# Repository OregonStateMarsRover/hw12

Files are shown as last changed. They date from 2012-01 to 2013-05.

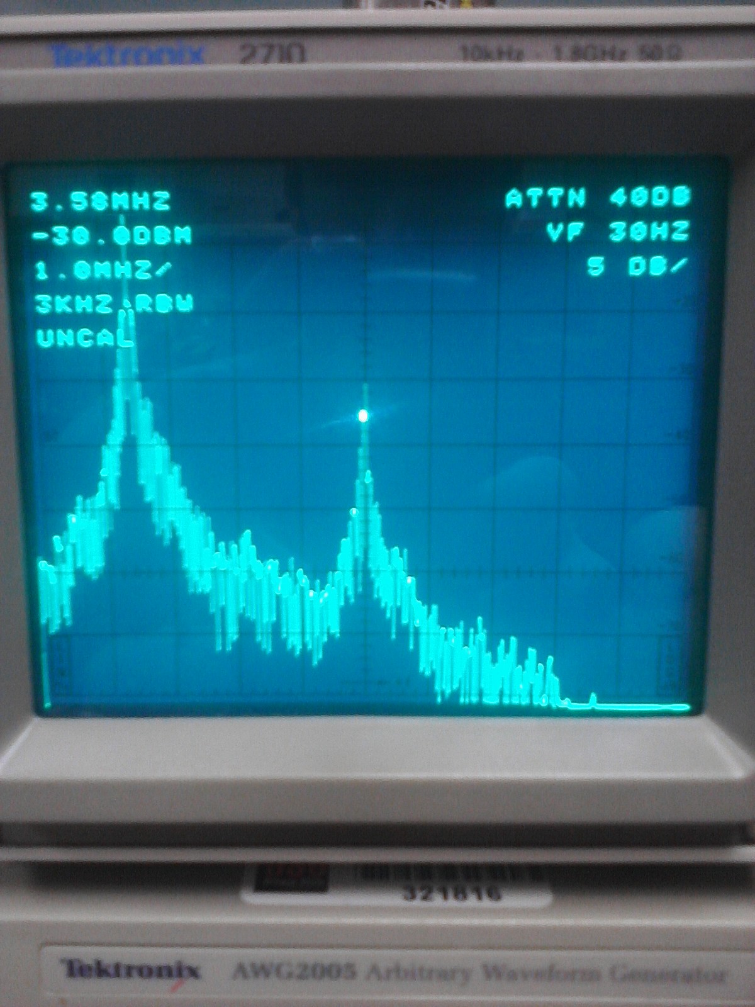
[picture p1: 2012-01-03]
electrical/design/RF&Video/UHF_Video_TX/documents/NTSCSpectrum.jpg

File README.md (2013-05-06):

How this repository is organized
====================

Electrical board documentation
------------------------
This should all be in electrical/design/.
There should be a folder for each board, containing the datasheets for the parts on the board.
There should be PADS drawings, and PDFs of both the schematic and the layout, and a text file BOM.
There should be an explanation of what the board does, and a list of the commercial parts that
it connects to. If there is a good way of linking to the datasheets for these parts, then we
might do that as well.

Commercial parts
-------------------
Parts that aren't custom built (motors, sensors, motor controllers, etc) should be in documents.
These will be further organized by folder.

Currently there are some issues
------------------
Things aren't all where they should be, and often there's three places to look for something.
We're working on that.  However, I don't intend to touch the mechanical folder.

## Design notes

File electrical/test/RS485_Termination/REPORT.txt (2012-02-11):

The purpose of this test is to determine the appropriate method of termination for RS-485 signaling through CAT5 with the SN65HVD32 as
the signal source.

test1a.csv:
	Source Termination: NONE
	Load Termination: 100ohms
	Measurement: Load
	Notes: Almost no ringing. DC current draw 33mA.
test1b.csv:
	Source Termination: NONE
	Load Termination: 100ohms
	Measurement: Source
	Notes: Small overshoot, pretty much as good as it can be.

test2a.csv:
	Source Termination: NONE
	Load Termination: NONE
	Measurement: Load
	Notes: Ringing, 210mV of overshoot.
test2b.csv:
	Source Termination: NONE
	Load Termination: NONE
	Measurement: Source
	Notes: Ringing, 210mV of overshoot.

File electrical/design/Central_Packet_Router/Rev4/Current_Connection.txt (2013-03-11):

Rev 3.
	Daugther Boards
		Motor Drivers
			Back Bogie  (J6)
			Left Bogie  (J12)
			Right Bogie (J7)
			Arm Board   (J2)
	I2C Breakout(Not Used Currently) (J205)
	Random Unused GPIO Pins On Headers (J206 & J207)		
	Freewave Connections (J3)
	UART Wiring
		UART 1: TX and RX Arm
		UART 2: TX and RX Int
		UART 4:	TX and RX Bogie
		UART 5:	TX and RX Freewave

Rev 4.
	Tripod Board
	Arm Contoller

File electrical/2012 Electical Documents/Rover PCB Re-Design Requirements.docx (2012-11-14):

- Tripod
  - redesign audio
  - use better servo connector
  - better video connector solution
  - look at power supply situation
  - reduce size
- Main board
  - remove audio
  - USB interface
  - DMA for GPS data?
    - email Francis about situation
  - No sensors
  - switch to linear regulators
    - simplify power requirements in general
  - Garmin GPS reveiver again

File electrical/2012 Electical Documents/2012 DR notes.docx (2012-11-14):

- CPC
  - Why use an and gate on the bogie RX without drivers with enable?
  - XTAL load capacitor Cl = (C^2/2C)+Cs, 26pF is correct capacitance
- Xbee
  - Reset controlled by MCU?
  - Header on TTL side of serial interface?
  - Test points
  - Thermal vias around LDO?
  - Ferrite beads?
  - AC termination
  - Screw keepouts top and bottom
  - SMA clearance
  - Machine pin header?
- Packet Router
  - Test points
  - Sink LEDs
  - Reset pullup
  - Diode on USB power
  - Series termination
  - Serial Isolation
  - Smaller series resistance on GPIO
  - Discrete resistors for GPIO current limiting
  - Ground USB connector shield
- Motor controller
  - Isolation between itself and sabertooth
  - Hall effect current sensor instead of current sense resistor
  - Smaller fuse
  - Match sabertooth terminal block pattern
  - Consider higher thickness PCB plating
- Solenoid Driver
  - Reduce complexity
  - Relays?

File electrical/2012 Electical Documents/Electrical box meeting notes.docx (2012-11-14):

Try mounting video mux to the top of the FM transmitter.

Try removing the modulator and PA and putting them in another enclosure.

Make faraday cage for mux.

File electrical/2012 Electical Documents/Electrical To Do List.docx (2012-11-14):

- EMI Testing
  - Cody / Tyler
- Main Board Redesign
  - Cody
- Camera Board Redesign
  - Tyler
- Critical Frequency List
  - Cody / Tyler
- Power Consumption Data Sheet
- Dr Hurst NSF Grant
  - Tyler / Delegated to John. Z?
- Figure Out Motor!!!
- Test Small Cameras
  - Tyler
- Test Motor Controllers
  - Cody / Tyler
- Figure Out Connectors
  - Everyone

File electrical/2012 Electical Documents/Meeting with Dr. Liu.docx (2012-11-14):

- Automatic antenna pointing device
  - GPS based angle
- MIMO with best antenna selection circuit
- Possibly implement automatic bitrate scaling
- Don’t try to use davinci
- Come up with repeater system

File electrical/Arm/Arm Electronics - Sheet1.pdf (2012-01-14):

Joint 2
| 2 | Limit Switch | http://www.mouser.com/catalog/specsheets/E51_Series.pdf
| 1 | Gear motor | https://docs.google.com/viewer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
| 1 | Magnetic Encoder (RMB30SI) | http://www.rls.si/document/RMB30D01.pdf

Joint 3
| 1 | 300 deg Potentiometer (P232) | http://www.bitechnologies.com/pdfs/p232.pdf
| 1 | AX-12 | http://www.crustcrawler.com/products/bioloid/docs/AX-12.pdf

Interchangable Joints

Configuration 1 (Equipment Servicing)

| 1 | 300 deg Potentiometer (P232) | http://www.bitechnologies.com/pdfs/p232.pdf
| 1 | AX-12 | http://www.crustcrawler.com/products/bioloid/docs/AX-12.pdf
| 2 | Voltage Reading Plates
| 1 | Vibration Motor | http://www.mouser.com/ProductDetail/Autotrol/052-0010AD/?qs=sGAEpiMZZMvuFyKEiodORsPMp4IpwWQM9fx3Xx3cERs%3d | *This is a 12VDC motor, but we can run it on the 9.5 Rail voltage for the AX-12s
| 3 | Pin Hole Camera | TBD

Configuration 2 (Soil Sample)

| 1 | AX-12 | http://www.crustcrawler.com/products/bioloid/docs/AX-12.pdf
| 1 | Pin Hole Camera | TBD
| QTY. | Part Description | DataSheet
Joint 1
| 2 | Limit Switch | http://www.mouser.com/catalog/specsheets/E51_Series.pdf
| 1 | Gear motor | https://docs.google.com/viewer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
| 1 | Magnetic Encoder (RMB300SI) | http://www.rls.si/document/RMB30D01.pdf

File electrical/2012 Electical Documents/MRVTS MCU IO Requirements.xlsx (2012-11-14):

Function | Interface(s) | GPIO Pins | USARTs | CLK Pins | ADC | '+ | Total GPIO | Total USARTs | Total CLK | Total ADC
Leveling Amplifier Gain | GPIO | 4 |  |  |  | '+ | 30 | 3 | 2 | 4
Leveling Amplifier PED | ADC |  |  |  | 2 | '+
RS485 TRX | UART, GPIO | 2 | 1 |  |  | '+
PLL | SPI, GPIO | 3 | 1 | 1 |  | '+
PLL Lock LED | GPIO | 1 |  |  |  | '+
VSWR OK LED | GPIO | 1 |  |  |  | '+
TEMP OK LED | GPIO | 1 |  |  |  | '+
'+3.6V Enable | GPIO | 1 |  |  |  | '+
'+6V Enable | GPIO | 1 |  |  |  | '+
PA ON LED | GPIO | 1 |  |  |  | '+
MUX | GPIO | 8 |  |  |  | '+
BDC PED | ADC |  |  |  | 2 | '+
TEMP Sensor | SPI | 1 | 1 | 1 |  | '+
PA Enable | GPIO | 1 |  |  |  | '+
PA Gain SEL | GPIO | 4 |  |  |  | '+
Video Buffer Enable | GPIO | 1 |  |  |  | '+
 |  |  |  |  |  | '+
 |  |  |  |  |  | '+
 |  |  |  |  |  | '+
 |  |  |  |  |  | '+
 |  |  |  |  |  | '+
 |  |  |  |  |  | '+
 |  |  |  |  |  | '+
 |  |  |  |  |  | '+
 |  |  |  |  |  | '+
 |  |  |  |  |  | '+
 |  |  |  |  |  | '+
 |  |  |  |  |  | '+
 |  |  |  |  |  | '+
 |  |  |  |  |  | '+
 |  |  |  |  |  | '+
 |  |  |  |  |  | '+
 |  |  |  |  |  | '+
 |  |  |  |  |  | '+
 |  |  |  |  |  | '+
 |  |  |  |  |  | '+
 |  |  |  |  |  | '+
 |  |  |  |  |  | '+
 |  |  |  |  |  | '+
 |  |  |  |  |  | '+
 |  |  |  |  |  | '+
 |  |  |  |  |  | '+
 |  |  |  |  |  | '+
 |  |  |  |  |  | '+
 |  |  |  |  |  | '+
 |  |  |  |  |  | '+
 |  |  |  |  |  | '+
 |  |  |  |  |  | '+
 |  |  |  |  |  | '+
 |  |  |  |  |  | '+
 |  |  |  |  |  | '+
 |  |  |  |  |  | '+
 |  |  |  |  |  | '+
 |  |  |  |  |  | '+
 |  |  |  |  |  | '+
 |  |  |  |  |  | '+
 |  |  |  |  |  | '+
 |  |  |  |  |  | '+
 |  |  |  |  |  | '+
 |  |  |  |  |  | '+
 |  |  |  |  |  | '+
 |  |  |  |  |  | '+
 |  |  |  |  |  | '+
 |  |  |  |  |  | '+
 |  |  |  |  |  | '+
 |  |  |  |  |  | '+
 |  |  |  |  |  | '+
 |  |  |  |  |  | '+
 |  |  |  |  |  | '+
 |  |  |  |  |  | '+
 |  |  |  |  |  | '+
 |  |  |  |  |  | '+
 |  |  |  |  |  | '+
 |  |  |  |  |  | '+
 |  |  |  |  |  | '+
 |  |  |  |  |  | '+
 |  |  |  |  |  | '+
 |  |  |  |  |  | '+
 |  |  |  |  |  | '+
 |  |  |  |  |  | '+
 |  |  |  |  |  | '+
 |  |  |  |  |  | '+
 |  |  |  |  |  | '+
 |  |  |  |  |  | '+
 |  |  |  |  |  | '+
 |  |  |  |  |  | '+
 |  |  |  |  |  | '+
 |  |  |  |  |  | '+
 |  |  |  |  |  | '+
 |  |  |  |  |  | '+
 |  |  |  |  |  | '+
 |  |  |  |  |  | '+
 |  |  |  |  |  | '+
 |  |  |  |  |  | '+
 |  |  |  |  |  | '+
 |  |  |  |  |  | '+
 |  |  |  |  |  | '+
 |  |  |  |  |  | '+
 |  |  |  |  |  | '+
 |  |  |  |  |  | '+
 |  |  |  |  |  | '+
 |  |  |  |  |  | '+
 |  |  |  |  |  | '+

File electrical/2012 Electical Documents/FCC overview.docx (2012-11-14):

Oregon State University

2012 URC

RF Communication Systems & FCC Licensing Overview

Still Image Transmission System

- Communications standard
  - IEEE 802.15.4
- Operating bandwidth
  - 2.4000GHz - 2.4835GHz
- RF transmission in specified bandwidth
  - YES
- RF reception in specified bandwidth
  - YES
- Transmission power
  - +17.8dBm
- Vehicle ERP
  - +23.8dBm
- Base station ERP
  - +29.8dBm
- Duty cycle
  - Intermittent transmission during operation
  - Inactive on demand
- FCC bandwidth allocation
  - ISM
- FCC licensing requirements
  - None

Video Transmission System

- Communications standard
  - Analog FM
- Operating bandwidth
  - 980MHz - 1040MHz
- RF transmission in specified bandwidth
  - YES
- RF reception in specified bandwidth
  - NO
- Transmission power
  - +37dBm
- Vehicle ERP
  - +43dBm
- Duty cycle
  - Always transmitting during operation
  - Inactive on demand
- FCC bandwidth allocation
  - Aeronautical radionavigation
- FCC licensing requirements
  - Technician's license required
  - License holder: Matt Shuman

Control & Telemetry Transmission System

- Communication standard
  - Proprietary FHSS
- Operating bandwidth
  - 2.4000GHz - 2.4835GHz
- Transmission power
  - +30dBm
- Vehicle ERP
  - +36dBm
- Base station ERP
  - +42dBm
- Duty cycle
  - Intermittent transmission during operation
  - Inactive on demand
- FCC bandwidth allocation
  - ISM
- FCC licensing requirements
  - None

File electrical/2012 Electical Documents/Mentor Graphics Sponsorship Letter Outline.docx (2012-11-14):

1 Status of last year’s competition
  a What went poorly
    i Video transmission system
    ii Reliability of motion control system
    iii Operator error
  b What went well
    i Site Survey

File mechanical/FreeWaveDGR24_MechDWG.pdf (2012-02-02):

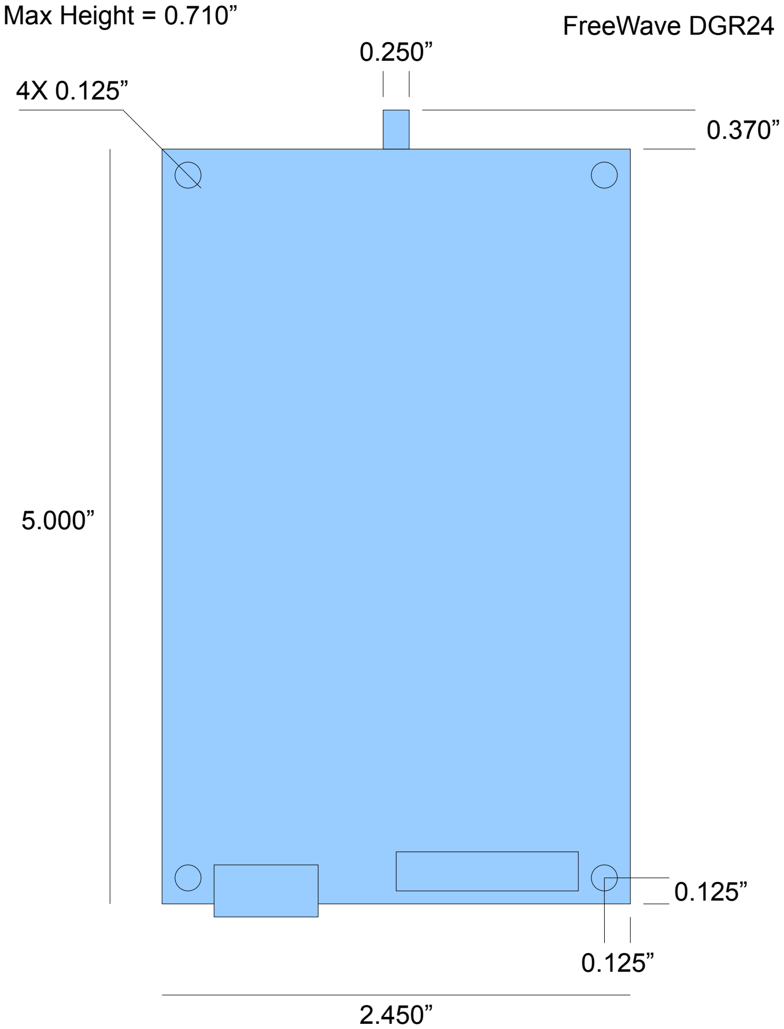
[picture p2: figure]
Max Height = 0.710”; FreeWave DGR24

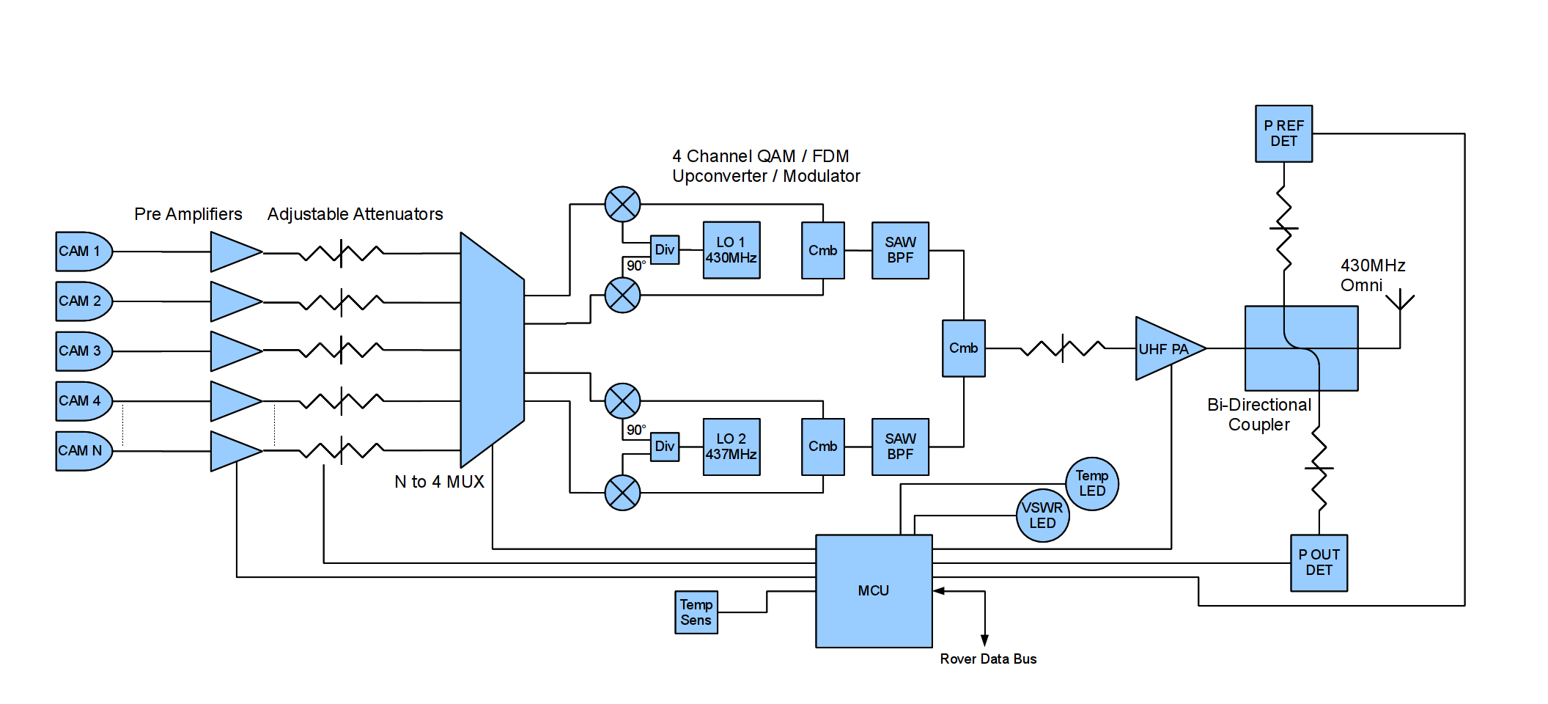
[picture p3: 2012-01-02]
electrical/design/RF&Video/UHF_Video_TX/documents/4channelVideoTX.png

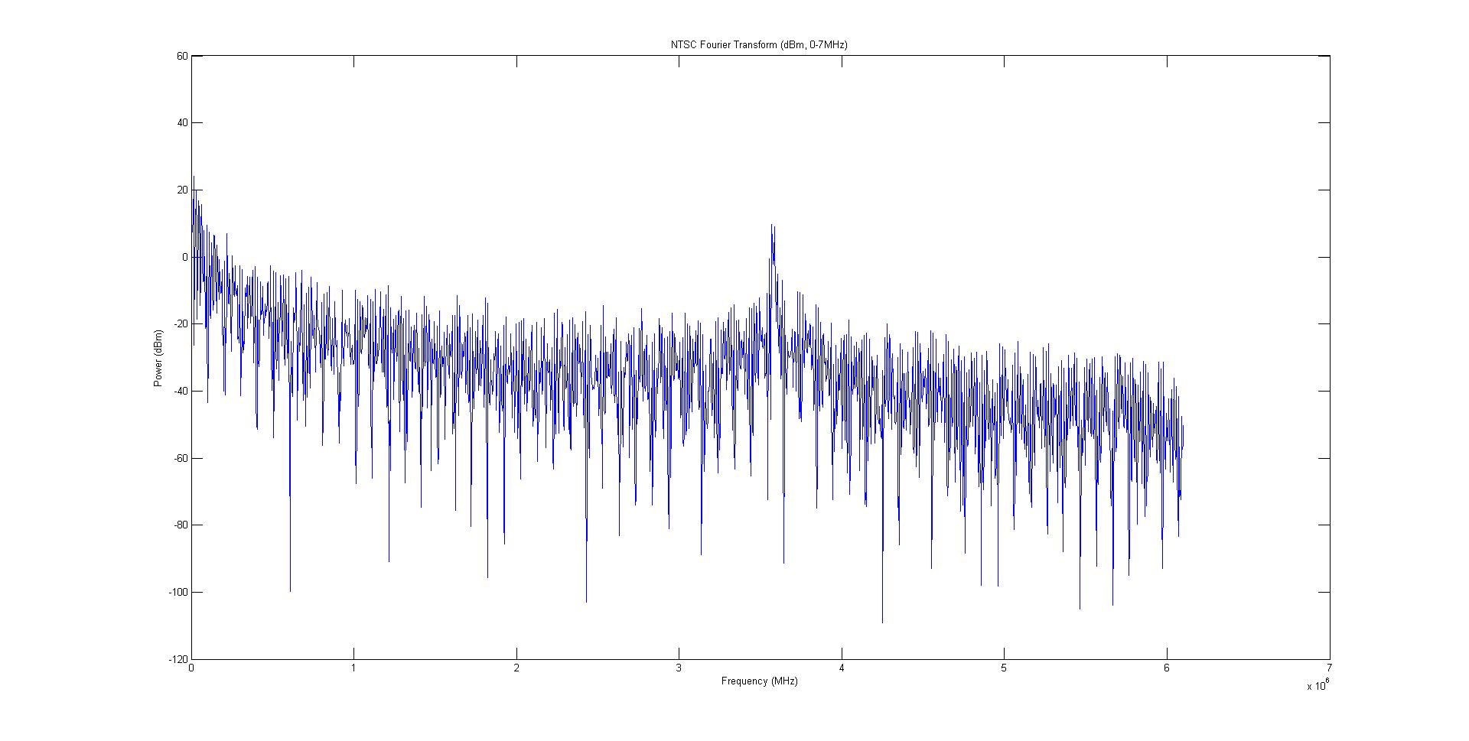
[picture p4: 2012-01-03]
electrical/design/RF&Video/UHF_Video_TX/documents/ntscSpectrum (2).jpg

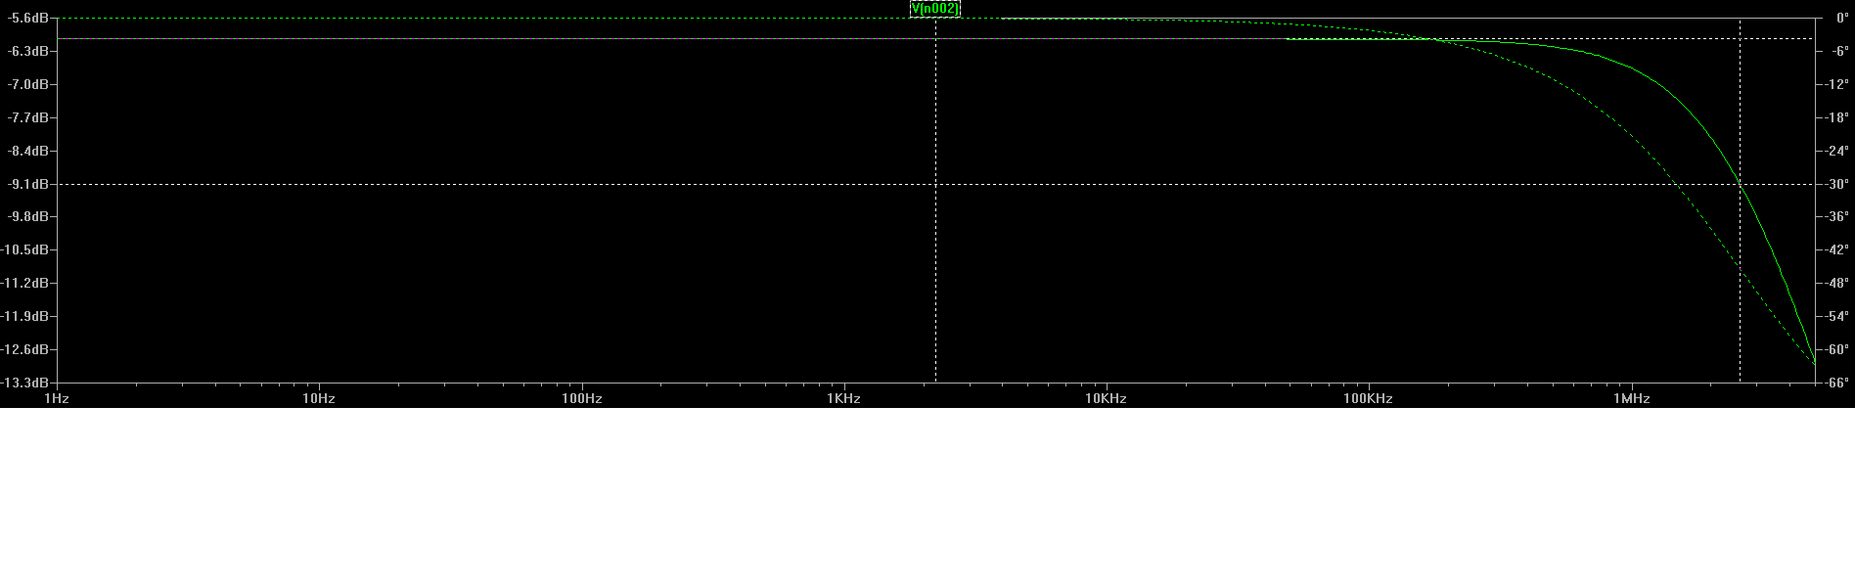
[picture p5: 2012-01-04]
electrical/design/RF&Video/UHF_Video_TX/documents/X9313WSI_bode.png

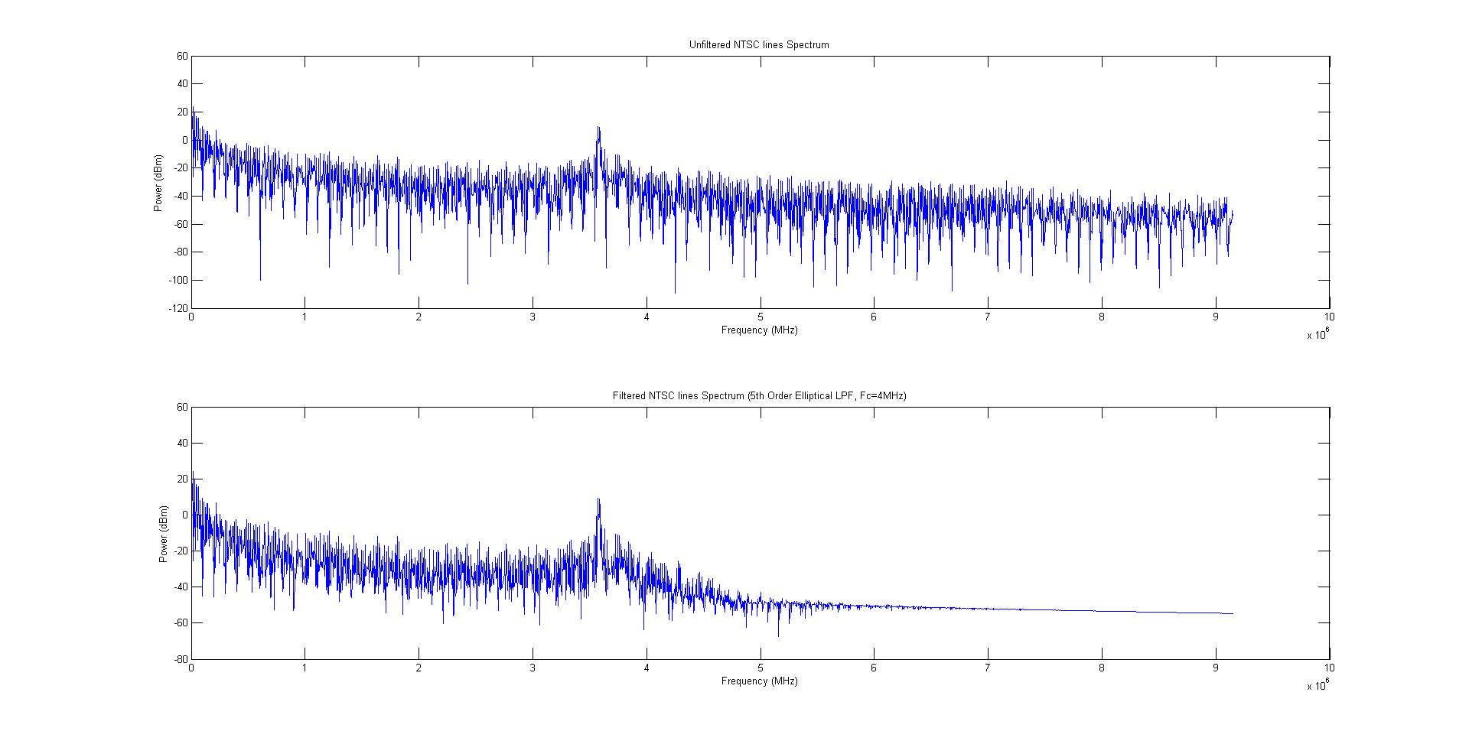
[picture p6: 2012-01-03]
electrical/design/RF&Video/UHF_Video_TX/documents/inputFilter.jpg

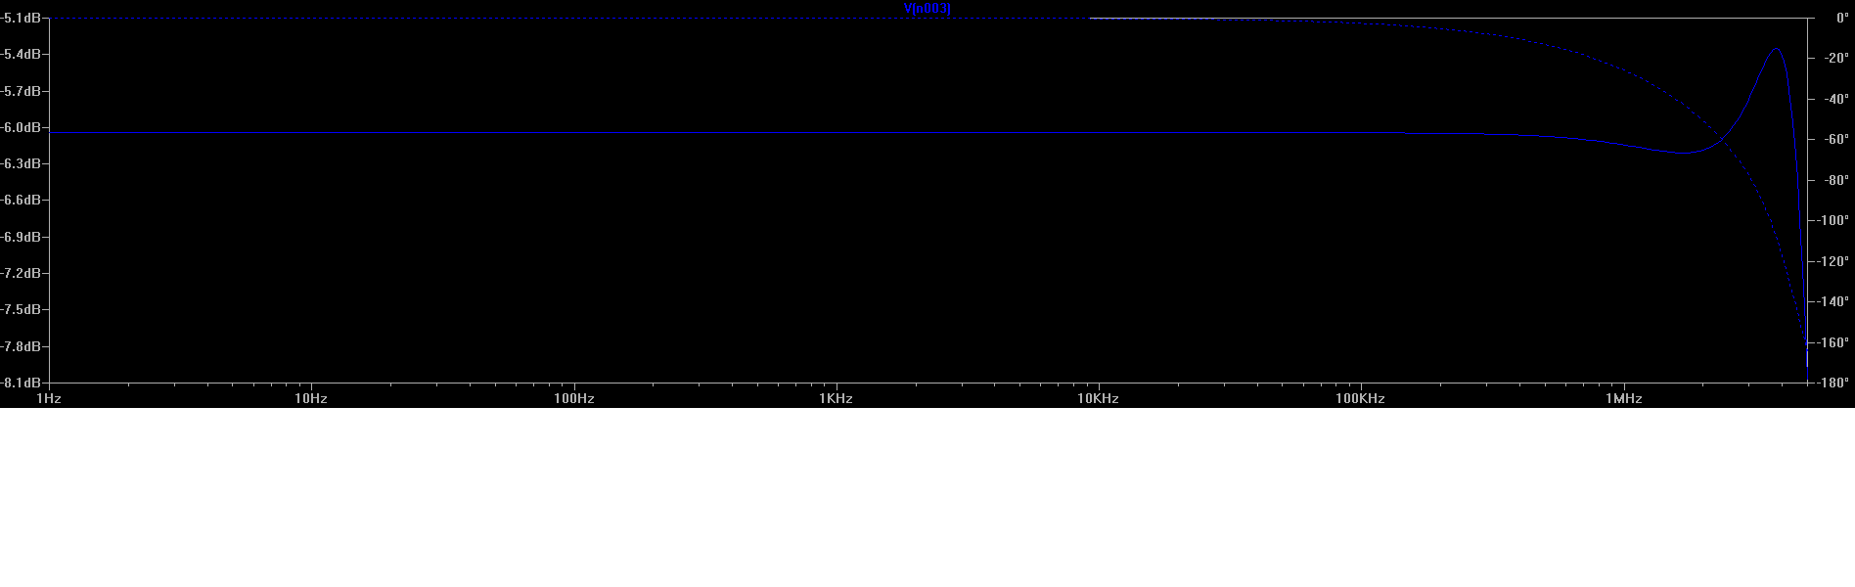
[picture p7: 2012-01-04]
electrical/design/RF&Video/UHF_Video_TX/documents/X9313WSI_compensated_bode.png

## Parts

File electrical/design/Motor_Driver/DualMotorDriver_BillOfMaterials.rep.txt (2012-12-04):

|-----------------------------------------------------------------------|
|Bill Of Materials for DualMotorDriver.sch on Tue Dec 04 11:28:17 2012  |
|-----------------------------------------------------------------------|
|Item|Qty |Reference|Part Name     |Description                  |Value |
|----+----+---------+--------------+-----------------------------+------|
|1   |1   |Y1       |ABL-16.000MHZ-|XTAL, THT, 16.000MHz         |16.000|
|    |    |         |B2,16.000MHz  |                             |MHz   |
|2   |1   |L1       |ACML-0603-190 |Ferrite Bead, 0603           |      |
|3   |1   |U1       |ATXMEGA16D4   |ATxmega D4 series MCU - 16k  |      |
|    |    |         |              |flash                        |      |
|4   |11  |C1-4 C9  |CAP-0603,0.1uF|Capacitor, SMT, 0603         |0.1uF |
|    |    |C11-13   |              |                             |      |
|    |    |C308     |              |                             |      |
|    |    |C310-311 |              |                             |      |
|5   |1   |C306     |CAP-0603,1.2nF|Capacitor, SMT, 0603         |1.2nF |
|6   |4   |C20-23   |CAP-0603,10pF |Capacitor, SMT, 0603         |10pF  |
|7   |1   |C305     |CAP-0603,15nF |Capacitor, SMT, 0603         |15nF  |
|8   |2   |C7-8     |CAP-0603,18pF |Capacitor, SMT, 0603         |18pF  |
|9   |1   |C307     |CAP-0603,1pF  |Capacitor, SMT, 0603         |1pF   |
|10  |1   |C10      |CAP-0603,1uF  |Capacitor, SMT, 0603         |1uF   |
|11  |2   |C5-6     |CAP-0603,4.7uF|Capacitor, SMT, 0603         |4.7uF |
|12  |2   |C309 C312|CAP-1206,10uF |SURFACE MOUNT CAPACITOR 0.062|10uF  |
|    |    |         |              |X 0.126 INCHES               |      |
|13  |4   |C16-19   |CAP-1206,4.7uF|SURFACE MOUNT CAPACITOR 0.062|4.7uF |
|    |    |         |              |X 0.126 INCHES               |      |
|14  |1   |C304     |CAP-1210,4.7uF|Capacitor, SMT, 1206         |4.7uF |
|15  |2   |C24-25   |CAP-RADIAL-10X|Radial Electrolytic          |470uF |
|    |    |         |12.5_3MMP,    |Capacitor, 10x12.5x3mm       |      |
|    |    |         |470uF         |(DxHxP)                      |      |
|16  |1   |C303     |CAP-RADIAL-6.3|Radial Electrolytic          |NU    |
|    |    |         |X7_2.5MMP,NU  |Capacitor, 6.3x7x2.5mm       |      |
|    |    |         |              |(DxHxP)                      |      |
|17  |1   |F1       |FUSE_HOLDER_35|Automotive Fuse Holder       |      |
|    |    |         |44-2          |                             |      |
|18  |3   |J3       |HDR_2P1R_100MI|Standard 2 Pin 1 Row .100"   |      |
|    |    |T300-301 |L             |Header                       |      |
|19  |1   |J1       |HDR_PDI_6_COMP|Header, 6P 2 Row, Through    |      |
|    |    |         |ACT           |Hole, Shroded, 100x100mil,   |      |
|    |    |         |              |for ISP-6 Programming        |      |
|20  |1   |J2       |HDR_SHERLOCK_5|Molex Sherlock 2.0mm         |      |
|    |    |         |P_V           |Header-5P Vertical           |      |
|21  |2   |J5 J300  |HDR_TERMBLOCK_|Screw Terminal Block,        |      |
|    |    |         |5MM-2P        |Horizontal, 5mm, 2 pos.      |      |
|22  |1   |U3       |HIP4082IBZ    |Full Bridge NMOS Gate Driver |      |
|23  |1   |L300     |IND_ELL-6UH470|47uH SMT inductor, shielded, |47uH  |
|    |    |         |M,47uH        |900mA max DC                 |      |
|24  |1   |U4       |MAX4372T      |High-side current sense      |      |
|    |    |         |              |amplifier, 0-28V             |      |
|25  |4   |X1-4     |PHOLE-#4      |Mounting Hole #4 Screw       |      |
|26  |4   |Q1-4     |PSMN011-80YS  |N-Ch MOSFET, 80V 67A 11mOhm, |      |
|    |    |         |              |LFPAK                        |      |
|27  |4   |R3-4 R7-8|RES-0603,1    |SURFACE MOUNT RESISTOR 0.031 |1     |
|    |    |         |              |X 0.061 INCHES, 1/10W        |      |
|28  |2   |R1 R10   |RES-0603,100k |SURFACE MOUNT RESISTOR 0.031 |100k  |
|    |    |         |              |X 0.061 INCHES, 1/10W        |      |
|29  |1   |R5       |RES-0603,10K  |SURFACE MOUNT RESISTOR 0.031 |10K   |
|    |    |         |              |X 0.061 INCHES, 1/10W        |      |
|30  |1   |R305     |RES-0603,10k  |SURFACE MOUNT RESISTOR 0.031 |10k   |
|    |    |         |              |X 0.061 INCHES, 1/10W        |      |
|31  |1   |R302     |RES-0603,165k |SURFACE MOUNT RESISTOR 0.031 |165k  |
|    |    |         |              |X 0.061 INCHES, 1/10W        |      |
|32  |2   |R303-304 |RES-0603,53.6k|SURFACE MOUNT RESISTOR 0.031 |53.6k |
|    |    |         |              |X 0.061 INCHES, 1/10W        |      |
|33  |2   |R9 R11   |RES-0603,5k   |SURFACE MOUNT RESISTOR 0.031 |5k    |
|    |    |         |              |X 0.061 INCHES, 1/10W        |      |
|34  |1   |R6       |RES-0603,???  |SURFACE MOUNT RESISTOR 0.031 |???   |
|    |    |         |              |X 0.061 INCHES, 1/10W        |      |
|35  |1   |R2       |RES-2512,0.01 |2512 SMD Resistor            |0.01  |
|36  |5   |D1-4 D300|SCH_CD214A-B36|Diode, Schottky, 3A 60V, SMA |0.7V  |
|    |    |         |0LF,0.7V      |                             |      |
|37  |2   |D5-6     |SCH_PMEG6002EJ|Schottky Diode, 60V, 2.75A,  |      |
|    |    |         |              |SOD-323F                     |      |
|38  |1   |U2       |SN65HVD32     |TXR,485 Full Duplex          |      |
|39  |1   |S1       |SW_SPST_SWT6-E|Tactile Pushbutton, SPST, 6mm|      |
|    |    |         |5M            |                             |      |
|40  |1   |U301     |TPS5401       |Integrated Buck Converter,   |      |
|    |    |         |              |0.5A Max, 42V In Max         |      |
|41  |1   |U302     |TPS79333      |3.3V LDO, 200mA Maximum      |      |
|    |    |         |              |current                      |      |
|-----------------------------------------------------------------------|

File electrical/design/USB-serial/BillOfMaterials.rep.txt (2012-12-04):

|-----------------------------------------------------------------------|
|Bill Of Materials for usb-serial1.sch on Tue Dec 04 11:32:23 2012      |
|-----------------------------------------------------------------------|
|Item|Qty |Reference|Part Name     |Description                  |Value |
|----+----+---------+--------------+-----------------------------+------|
|1   |8   |C1-8     |CAP-0603,0.1uF|Capacitor, SMT, 0603         |0.1uF |
|2   |1   |U1       |FT230XS-R     |USB-Serial UART Bridge,      |      |
|    |    |         |              |SSOP-16                      |      |
|3   |1   |J7       |HDR_1R4P_100MI|100 mil 4x1 header footprint |      |
|    |    |         |L             |                             |      |
|4   |5   |J2-4 J6  |HDR_2P1R_100MI|Standard 2 Pin 1 Row .100"   |      |
|    |    |J8       |L             |Header                       |      |
|5   |1   |J5       |HDR_SHERLOCK_5|Molex Sherlock 2.0mm         |      |
|    |    |         |P_RA          |Header-5P Vertical           |      |
|6   |1   |J1       |HDR_USB_154-15|USB Header Mini-B Type,      |      |
|    |    |         |320-E         |Female                       |      |
|7   |1   |J9       |K22X-E9P-N    |Header, DE9, Male, Right     |      |
|    |    |         |              |Angle Through Hole           |      |
|8   |3   |D1-3     |LED_0603_GREEN|LED, 0603, Green             |      |
|9   |2   |R7-8     |RES-0603,10k  |SURFACE MOUNT RESISTOR 0.031 |10k   |
|    |    |         |              |X 0.061 INCHES, 1/10W        |      |
|10  |2   |R1-2     |RES-0603,22   |SURFACE MOUNT RESISTOR 0.031 |22    |
|    |    |         |              |X 0.061 INCHES, 1/10W        |      |
|11  |3   |R4-6     |RES-0603,500  |SURFACE MOUNT RESISTOR 0.031 |500   |
|    |    |         |              |X 0.061 INCHES, 1/10W        |      |
|12  |1   |R3       |RES-0603,RT   |SURFACE MOUNT RESISTOR 0.031 |RT    |
|    |    |         |              |X 0.061 INCHES, 1/10W        |      |
|13  |1   |U2       |SN65HVD35     |Full Duplex RS-485           |      |
|    |    |         |              |Transceiver w/ Enables, 3.3V,|      |
|    |    |         |              |SOIC14                       |      |
|14  |1   |U3       |TRS3221E      |RS-232 Line Driver, 1MBps,   |      |
|    |    |         |              |3-5.5V VCC                   |      |
|-----------------------------------------------------------------------|

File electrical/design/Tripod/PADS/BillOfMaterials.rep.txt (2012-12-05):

|-----------------------------------------------------------------------|
|Bill Of Materials for tripod.sch on Tue Nov 27 16:17:03 2012           |
|-----------------------------------------------------------------------|
|Item|Qty |Reference|Part Name     |Description                  |Value |
|----+----+---------+--------------+-----------------------------+------|
|1   |1   |J2       |142146-75     |SMB, Right Angle             |      |No
|2   |1   |U33      |74LVC1G126GV  |Buffer, Tri-State, Single    |      |No
|3   |1   |Y1       |ABM2-16.000MHZ|Crystal                      |      |Yes
|    |    |         |-D4Y-T        |                             |      |
|4   |1   |M1       |AOM-6545P-R   |                             |      |Yes
|5   |1   |U4       |ATXMEGA128A3  |MCU, 8/16b,AVR,              |      |Yes
|    |    |         |              |ATXMega128A3AU               |      |
|6   |21  |D1 D3-12 |B72500D0050A06|Bidirectional TVS Diode      |      |Yes
|    |    |D14-16   |0             |                             |      |
|    |    |D18-24   |              |                             |      |
|7   |1   |U3       |BMP085        |Barometric Pressure Sensor   |      |No
|8   |16  |C3-6     |CAP-0603,     |Capacitor                    |0.1uF |No
|    |    |C15-16   |0.1uF,10%     |                             |      |
|    |    |C24 C33  |              |                             |      |
|    |    |C43-47   |              |                             |      |
|    |    |C105 C111|              |                             |      |
|    |    |C116     |              |                             |      |
|9   |2   |C103 C109|CAP-0603,10nF,|Capacitor                    |10nF  |
|    |    |         |5%            |                             |      |
|10  |7   |C7-8     |CAP-0603,10uF,|Capacitor                    |10uF  |
|    |    |C10-13   |10%           |                             |      |
|    |    |C19      |              |                             |      |
|11  |2   |C22 C25  |CAP-0603,22nF,|Capacitor                    |22nF  |
|    |    |         |20%           |                             |      |
|12  |3   |C1-2 C51 |CAP-0603,27pF,|Capacitor                    |27pF  |
|    |    |         |5%            |                             |      |
|13  |2   |C9 C20   |CAP-0603,     |Capacitor                    |4.7uF |
|    |    |         |4.7uF,20%     |                             |      |
|14  |2   |C17 C23  |CAP-0805,10uF,|Capacitor                    |10uF  |
|    |    |         |10%           |                             |      |
|15  |2   |C26-27   |CAP-0805,1uF, |Capacitor                    |1uF   |
|    |    |         |10%           |                             |      |
|16  |3   |C104 C110|CAP-1206,10uF,|Capacitor                    |10uF  |
|    |    |C113     |10%           |                             |      |
|17  |3   |C14 C18  |CAP_RAD_10X16M|Capacitor                    |470uF |
|    |    |C21      |M,470uF,20%   |                             |      |
|18  |1   |L1       |CHOKE,39mH,5% |Choke, Sheilded              |39mH  |No
|19  |1   |U5       |DRV135        |Balanced Audio Line Driver   |      |Yes
|20  |1   |J1       |FFC_6200097   |                             |      |
|21  |1   |J5       |HDR_MINIFIT_2R|Header, 4 Pin 2 Row Minifit  |      |
|    |    |         |4P_RA         |4.2mm Pitch, Right Angle     |      |
|22  |1   |J28      |HDR_PDI_6     |Header, 6P 2 Row, Through    |      |
|    |    |         |              |Hole, Shroded, 100x100mil,   |      |
|    |    |         |              |for ISP-6 Programming        |      |
|23  |1   |J3       |HDR_SHERLOCK_3|Molex Sherlock 2.0mm         |      |
|    |    |         |P_RA          |Header-3P Vertical           |      |
|24  |1   |J204     |HDR_SHERLOCK_5|Molex Sherlock 2.0mm         |      |
|    |    |         |P_V           |Header-5P Vertical           |      |
|25  |1   |J4       |HDR_SPOX_3P_V |Header, SPOX, 3P1R           |      |
|26  |1   |U35      |KXUD9-4100    |3 Axis Differential          |      |No
|    |    |         |              |Accertlerometer                |      |
|27  |3   |D2 D25   |LED-0805_DIALI|LED, 0805, Red               |      |
|    |    |D28      |GHT_598-8110-1|                             |      |
|    |    |         |07F           |                             |      |
|28  |2   |D13 D17  |LED-0805_DIALI|LED                          |      |
|    |    |         |GHT_598-8170-1|                             |      |
|    |    |         |07F           |                             |      |
|29  |1   |U8       |LM3480IM3X-5.0|Linear Regulator             |      |
|30  |1   |U7       |MAX864        |Dual Charge Pump             |      |No
|31  |1   |R5       |POT,100K,10%  |Trimmer Pot, Multiturn       |100K  |Yes
|32  |1   |U32      |REG103GA-5    |LDO Voltage Regulator        |      |Yes
|33  |1   |U31      |REG103GA-3.3  |LDO Voltage Regulator        |      |No
|34  |4   |R3 R14   |RES-0603,10K, |Resistor                     |10K   |
|    |    |R22-23   |1%            |                             |      |
|35  |4   |R11      |RES-0603,150, |Resistor                     |150   |
|    |    |R17-18   |1%            |                             |      |
|    |    |R109     |              |                             |      |
|36  |3   |R4 R12-13|RES-0603,1K,1%|Resistor                     |1K    |
|37  |1   |R10      |RES-0603,     |Resistor                     |2.43K |
|    |    |         |2.43K,1%      |                             |      |
|38  |1   |R115     |RES-0603,324, |Resistor                     |324   |
|    |    |         |1%            |                             |      |
|39  |9   |R1-2 R6  |RES-0603,4.7K,|Resistor                     |4.7K  |
|    |    |R15-16   |5%            |                             |      |
|    |    |R28      |              |                             |      |
|    |    |R119-121 |              |                             |      |
|40  |3   |R7-9     |RES-0603,OPT-0|Resistor                     |OPT-0 |
|41  |1   |U2       |SN65HVD35     |RS-485 Transceiver           |      |
|42  |1   |SW1      |SW_SKHHAMA010 |Tactile Push-button          |      |
|43  |1   |U1       |TL082         |Dual Op-Amp                  |      |Yes
|44  |21  |TPNT1-21 |TPNT          |Test point with via          |      |
|-----------------------------------------------------------------------|

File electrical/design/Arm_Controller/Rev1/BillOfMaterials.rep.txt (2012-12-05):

|-----------------------------------------------------------------------|
|Bill Of Materials for armctl1.sch on Tue Nov 27 16:15:26 2012          |
|-----------------------------------------------------------------------|
|Item|Qty |Reference|Part Name     |Description                  |Value |
|----+----+---------+--------------+-----------------------------+------|
|1   |1   |U205     |74HC1G14GV    |Schmitt Trigger Inverter     |      | No
|2   |1   |U201     |74LVC2G07_DCK |Dual Open Drain Schmitt      |      | Ordered
|    |    |         |              |Buffers, SC-70-6             |      |
|3   |1   |Y100     |ABM2-16.000MHZ|Crystal, 16.000MHz, SMD      |16.000| Yes
|    |    |         |-D4Y-T,       |                             |MHz   |
|    |    |         |16.000MHz     |                             |      |
|4   |1   |L100     |ACML-0603-190 |Ferrite Bead, 0603           |      | Ordered
|5   |1   |U100     |ATXMEGA16D4   |ATxmega D4 series MCU - 16k  |      | Yes
|    |    |         |              |flash                        |      | 
|6   |15  |C101-105 |CAP-0603,0.1uF|Capacitor, SMT, 0603         |0.1uF |
|    |    |C200-202 |              |                             |      |
|    |    |C206-209 |              |                             |      |
|    |    |C308     |              |                             |      |
|    |    |C310-311 |              |                             |      |
|7   |1   |C306     |CAP-0603,1.2nF|Capacitor, SMT, 0603         |1.2nF |
|8   |1   |C203     |CAP-0603,100pF|Capacitor, SMT, 0603         |100pF |
|9   |2   |C212-213 |CAP-0603,10nF |Capacitor, SMT, 0603         |10nF  |
|10  |1   |C305     |CAP-0603,15nF |Capacitor, SMT, 0603         |15nF  |
|11  |2   |C106-107 |CAP-0603,18pF |Capacitor, SMT, 0603         |18pF  |
|12  |4   |C204-205 |CAP-0603,1nF  |Capacitor, SMT, 0603         |1nF   |
|    |    |C210-211 |              |                             |      |
|13  |1   |C307     |CAP-0603,1pF  |Capacitor, SMT, 0603         |1pF   |
|14  |1   |C300     |CAP-0603,1uF  |Capacitor, SMT, 0603         |1uF   |
|15  |2   |C108-109 |CAP-0603,4.7uF|Capacitor, SMT, 0603         |4.7uF |
|16  |1   |C100     |CAP-0805,10uF |SURFACE MOUNT CAPACITOR 0.048|10uF  |
|    |    |         |              |X 0.079 INCHES               |      |
|17  |2   |C309 C312|CAP-1206,10uF |SURFACE MOUNT CAPACITOR 0.062|10uF  |
|    |    |         |              |X 0.126 INCHES               |      |
|18  |1   |C304     |CAP-1210,4.7uF|Capacitor, SMT, 1206         |4.7uF |
|19  |2   |C301-302 |CAP-RADIAL-10X|Radial Electrolytic          |330uF |
|    |    |         |12.5_3MMP,    |Capacitor, 10x12.5x3mm       |      |
|    |    |         |330uF         |(DxHxP)                      |      |
|20  |1   |C303     |CAP-RADIAL-6.3|Radial Electrolytic          |NU    |
|    |    |         |X7_2.5MMP,NU  |Capacitor, 6.3x7x2.5mm       |      |
|    |    |         |              |(DxHxP)                      |      |
|21  |1   |F300     |FUSE_HOLDER_35|Automotive Fuse Holder       |      |
|    |    |         |44-2          |                             |      |
|22  |6   |J100     |HDR_2P1R_100MI|Standard 2 Pin 1 Row .100"   |      |
|    |    |T200-202 |L             |Header                       |      |
|    |    |T300-301 |              |                             |      |
|23  |1   |J102     |HDR_PDI_6_COMP|Header, 6P 2 Row, Through    |      |
|    |    |         |ACT           |Hole, Shroded, 100x100mil,   |      |
|    |    |         |              |for ISP-6 Programming        |      |
|24  |2   |J201 J205|HDR_SHERLOCK_3|Molex Sherlock 2.0mm         |      |
|    |    |         |P_V           |Header-3P Vertical           |      |
|25  |1   |J202     |HDR_SHERLOCK_5|Molex Sherlock 2.0mm         |      |
|    |    |         |P_V           |Header-5P Vertical           |      |
|26  |2   |J203-204 |HDR_SHERLOCK_6|Header, Molex Sherlock,      |      |
|    |    |         |P_V           |2.0mm, 6 Pin, Vertical       |      |
|27  |2   |J200 J206|HDR_SHERLOCK_9|Header, Molex Sherlock,      |      |
|    |    |         |P_V           |2.0mm, 9 Pin, Vertical       |      |
|28  |2   |J300-301 |HDR_TERMBLOCK_|Screw Terminal Block,        |      |
|    |    |         |5MM-2P        |Horizontal, 5mm, 2 pos.      |      |
|29  |1   |L300     |IND_ELL-6UH470|47uH SMT inductor, shielded, |47uH  |
|    |    |         |M,47uH        |900mA max DC                 |      |
|30  |4   |D100     |LED_0603_GREEN|LED, 0603, Green             |      |
|    |    |D301-303 |              |                             |      |
|31  |1   |D101     |LED_0603_RED  |LED, 0603, Red               |      |
|32  |1   |Z100     |LM4040D25DBZR,|Precision 2.5V Shunt         |2.5V  |
|    |    |         |2.5V          |Reference                    |      |
|33  |1   |U206     |MAX3293       |RS-485 Transmitter, 250kbps, |      | No
|    |    |         |              |SOT23-6                      |      |
|34  |2   |U203-204 |MAX3281E      |Single RS-485 Receiver,      |      | Yes
|    |    |         |              |52Mbps, SOT23-6              |      |
|35  |1   |U300     |MAX4372T      |High-side current sense      |      | Yes
|    |    |         |              |amplifier, 0-28V             |      |
|36  |4   |X1-4     |PHOLE-#4      |Mounting Hole #4 Screw       |      |
|37  |1   |R203     |RES-0603,100  |SURFACE MOUNT RESISTOR 0.031 |100   |
|    |    |         |              |X 0.061 INCHES, 1/10W        |      |
|38  |9   |R100     |RES-0603,10k  |SURFACE MOUNT RESISTOR 0.031 |10k   |
|    |    |R200-202 |              |X 0.061 INCHES, 1/10W        |      |
|    |    |R204-207 |              |                             |      |
|    |    |R305     |              |                             |      |
|39  |2   |R208-209 |RES-0603,120  |SURFACE MOUNT RESISTOR 0.031 |120   |
|    |    |         |              |X 0.061 INCHES, 1/10W        |      |
|40  |1   |R302     |RES-0603,165k |SURFACE MOUNT RESISTOR 0.031 |165k  |
|    |    |         |              |X 0.061 INCHES, 1/10W        |      |
|41  |1   |R106     |RES-0603,1k   |SURFACE MOUNT RESISTOR 0.031 |1k    |
|    |    |         |              |X 0.061 INCHES, 1/10W        |      |
|42  |3   |R102-103 |RES-0603,390  |SURFACE MOUNT RESISTOR 0.031 |390   |
|    |    |R308     |              |X 0.061 INCHES, 1/10W        |      |
|43  |2   |R303-304 |RES-0603,53.6k|SURFACE MOUNT RESISTOR 0.031 |53.6k |
|    |    |         |              |X 0.061 INCHES, 1/10W        |      |
|44  |1   |R306     |RES-0603,6.2k |SURFACE MOUNT RESISTOR 0.031 |6.2k  |
|    |    |         |              |X 0.061 INCHES, 1/10W        |      |
|45  |1   |R307     |RES-0603,860  |SURFACE MOUNT RESISTOR 0.031 |860   |
|    |    |         |              |X 0.061 INCHES, 1/10W        |      |
|46  |1   |R101     |RES-0603,NU   |SURFACE MOUNT RESISTOR 0.031 |NU    |
|    |    |         |              |X 0.061 INCHES, 1/10W        |      |
|47  |1   |R300     |RES-2512,0.01 |2512 SMD Resistor            |0.01  |
|48  |1   |D300     |SCH_CD214A-B36|Diode, Schottky, 3A 60V, SMA |0.7V  | Yes
|    |    |         |0LF,0.7V      |                             |      |
|49  |1   |U202     |SN65HVD35     |Full Duplex RS-485           |      | Yes
|    |    |         |              |Transceiver w/ Enables, 3.3V,|      |
|    |    |         |              |SOIC14                       |      |
|50  |1   |U200     |SN74AHCT1G125_|Single TTL Buffer, SC-70-5   |      | yes
|    |    |         |DCK           |                             |      |
|51  |1   |S100     |SW_SPST_SWT6-E|Tactile Pushbutton, SPST, 6mm|      | yes
|    |    |         |5M            |                             |      |
|52  |1   |U301     |TPS5401       |Integrated Buck Converter,   |      | Ordered
|    |    |         |              |0.5A Max, 42V In Max         |      |
|53  |1   |U302     |TPS79333      |3.3V LDO, 200mA Maximum      |      | Ordered
|    |    |         |              |current                      |      |
|54  |6   |D200-205 |TVS_NUP2105LT1|Dual Bidirectional TVS Diode,|      | Yes
|    |    |         |G             |350W, SOT-23                 |      |
|-----------------------------------------------------------------------|

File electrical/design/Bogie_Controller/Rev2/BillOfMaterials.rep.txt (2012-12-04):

|--------------------------------------------------------------------------------------|
|Bill Of Materials for bogiectl3.sch on Sun Nov 25 15:34:11 2012                       |
|--------------------------------------------------------------------------------------|
|Item|Qty |Reference|Part Name     |Manufacturer  |Description                  |Value |
|----+----+---------+--------------+--------------+-----------------------------+------|
|1   |1   |U201     |74LVC2G07_DCK |              |Dual Open Drain Schmitt      |      |
|    |    |         |              |              |Buffers, SC-70-6             |      |
|2   |2   |U400-401 |74LVC2G34_DCK |              |Dual Schmitt Buffer, 5V      |      |
|    |    |         |              |              |Tolerant, SC-70-6            |      |
|3   |1   |Y100     |ABM2-16.000MHZ|Abracon       |Crystal, 16.000MHz, SMD      |16.000|
|    |    |         |-D4Y-T,       |              |                             |MHz   |
|    |    |         |16.000MHz     |              |                             |      |
|4   |1   |L100     |ACML-0603-190 |              |Ferrite Bead, 0603           |      |
|5   |1   |U100     |ATXMEGA16D4   |              |ATxmega D4 series MCU - 16k  |      |
|    |    |         |              |              |flash                        |      |
|6   |2   |C400-401 |CAP-0603,0.01u|              |Capacitor, SMT, 0603         |0.01u |
|7   |13  |C101-105 |CAP-0603,0.1uF|              |Capacitor, SMT, 0603         |0.1uF |
|    |    |C200-202 |              |              |                             |      |
|    |    |C308     |              |              |                             |      |
|    |    |C310-311 |              |              |                             |      |
|    |    |C402-403 |              |              |                             |      |
|8   |1   |C306     |CAP-0603,1.2nF|              |Capacitor, SMT, 0603         |1.2nF |
|9   |1   |C203     |CAP-0603,100pF|              |Capacitor, SMT, 0603         |100pF |
|10  |1   |C305     |CAP-0603,15nF |              |Capacitor, SMT, 0603         |15nF  |
|11  |2   |C106-107 |CAP-0603,18pF |              |Capacitor, SMT, 0603         |18pF  |
|12  |2   |C204-205 |CAP-0603,1nF  |              |Capacitor, SMT, 0603         |1nF   |
|13  |1   |C307     |CAP-0603,1pF  |              |Capacitor, SMT, 0603         |1pF   |
|14  |1   |C300     |CAP-0603,1uF  |              |Capacitor, SMT, 0603         |1uF   |
|15  |2   |C108-109 |CAP-0603,4.7uF|              |Capacitor, SMT, 0603         |4.7uF |
|16  |1   |C100     |CAP-0805,10uF |IPC SM-782    |SURFACE MOUNT CAPACITOR 0.048|10uF  |
|    |    |         |              |STD.          |X 0.079 INCHES               |      |
|17  |2   |C309 C312|CAP-1206,10uF |IPC SM-782    |SURFACE MOUNT CAPACITOR 0.062|10uF  |
|    |    |         |              |STD.          |X 0.126 INCHES               |      |
|18  |1   |C304     |CAP-1210,4.7uF|              |Capacitor, SMT, 1206         |4.7uF |
|19  |2   |C301-302 |CAP-RADIAL-10X|              |Radial Electrolytic          |330uF |
|    |    |         |12.5_3MMP,    |              |Capacitor, 10x12.5x3mm       |      |
|    |    |         |330uF         |              |(DxHxP)                      |      |
|20  |1   |C303     |CAP-RADIAL-6.3|              |Radial Electrolytic          |NU    |
|    |    |         |X7_2.5MMP,NU  |              |Capacitor, 6.3x7x2.5mm       |      |
|    |    |         |              |              |(DxHxP)                      |      |
|21  |1   |F300     |FUSE_HOLDER_35|Key Electric  |Automotive Fuse Holder       |      |
|    |    |         |44-2          |Co            |                             |      |
|22  |8   |J100     |HDR_2P1R_100MI|3M, Various   |Standard 2 Pin 1 Row .100"   |      |
|    |    |T200-202 |L             |              |Header                       |      |
|    |    |T300-301 |              |              |                             |      |
|    |    |T400-401 |              |              |                             |      |
|23  |1   |J102     |HDR_PDI_6_COMP|Molex         |Header, 6P 2 Row, Through    |      |
|    |    |         |ACT           |              |Hole, Shroded, 100x100mil,   |      |
|    |    |         |              |              |for ISP-6 Programming        |      |
|24  |1   |J201     |HDR_SHERLOCK_3|              |Molex Sherlock 2.0mm         |      |
|    |    |         |P_V           |              |Header-3P Vertical           |      |
|25  |2   |J400-401 |HDR_SHERLOCK_4|              |Molex Sherlock 2.0mm         |      |
|    |    |         |P_V           |              |Header-4P Vertical           |      |
|26  |3   |J200     |HDR_SHERLOCK_5|              |Molex Sherlock 2.0mm         |      |
|    |    |J202-203 |P_V           |              |Header-5P Vertical           |      |
|27  |2   |J300-301 |HDR_TERMBLOCK_|              |Screw Terminal Block,        |      |
|    |    |         |5MM-2P        |              |Horizontal, 5mm, 2 pos.      |      |
|28  |1   |L300     |IND_ELL-6UH470|              |47uH SMT inductor, shielded, |47uH  |
|    |    |         |M,47uH        |              |900mA max DC                 |      |
|29  |4   |D100     |LED_0603_GREEN|Lite-On       |LED, 0603, Green             |      |
|    |    |D301-303 |              |              |                             |      |
|30  |1   |D101     |LED_0603_RED  |Lite-On       |LED, 0603, Red               |      |
|31  |1   |Z100     |LM4040D25DBZR,|              |Precision 2.5V Shunt         |2.5V  |
|    |    |         |2.5V          |              |Reference                    |      |
|32  |1   |U300     |MAX4372T      |              |High-side current sense      |      |
|    |    |         |              |              |amplifier, 0-28V             |      |
|33  |4   |X1-4     |PHOLE-#4      |              |Mounting Hole #4 Screw       |      |
|34  |1   |R203     |RES-0603,100  |IPC SM-782    |SURFACE MOUNT RESISTOR 0.031 |100   |
|    |    |         |              |STD.          |X 0.061 INCHES, 1/10W        |      |
|35  |2   |R402-403 |RES-0603,100k |IPC SM-782    |SURFACE MOUNT RESISTOR 0.031 |100k  |
|    |    |         |              |STD.          |X 0.061 INCHES, 1/10W        |      |
|36  |7   |R100     |RES-0603,10k  |IPC SM-782    |SURFACE MOUNT RESISTOR 0.031 |10k   |
|    |    |R200-202 |              |STD.          |X 0.061 INCHES, 1/10W        |      |
|    |    |R204-205 |              |              |                             |      |
|    |    |R305     |              |              |                             |      |
|37  |1   |R302     |RES-0603,165k |IPC SM-782    |SURFACE MOUNT RESISTOR 0.031 |165k  |
|    |    |         |              |STD.          |X 0.061 INCHES, 1/10W        |      |
|38  |3   |R106     |RES-0603,1k   |IPC SM-782    |SURFACE MOUNT RESISTOR 0.031 |1k    |
|    |    |R400-401 |              |STD.          |X 0.061 INCHES, 1/10W        |      |
|39  |3   |R102-103 |RES-0603,390  |IPC SM-782    |SURFACE MOUNT RESISTOR 0.031 |390   |
|    |    |R308     |              |STD.          |X 0.061 INCHES, 1/10W        |      |
|40  |2   |R303-304 |RES-0603,53.6k|IPC SM-782    |SURFACE MOUNT RESISTOR 0.031 |53.6k |
|    |    |         |              |STD.          |X 0.061 INCHES, 1/10W        |      |
|41  |1   |R306     |RES-0603,6.2k |IPC SM-782    |SURFACE MOUNT RESISTOR 0.031 |6.2k  |
|    |    |         |              |STD.          |X 0.061 INCHES, 1/10W        |      |
|42  |1   |R307     |RES-0603,860  |IPC SM-782    |SURFACE MOUNT RESISTOR 0.031 |860   |
|    |    |         |              |STD.          |X 0.061 INCHES, 1/10W        |      |
|43  |1   |R101     |RES-0603,NU   |IPC SM-782    |SURFACE MOUNT RESISTOR 0.031 |NU    |
|    |    |         |              |STD.          |X 0.061 INCHES, 1/10W        |      |
|44  |1   |R300     |RES-2512,0.01 |              |2512 SMD Resistor            |0.01  |
|45  |1   |D300     |SCH_CD214A-B36|Bourns        |Diode, Schottky, 3A 60V, SMA |0.7V  |
|    |    |         |0LF,0.7V      |              |                             |      |
|46  |1   |U202     |SN65HVD35     |              |Full Duplex RS-485           |      |
|    |    |         |              |              |Transceiver w/ Enables, 3.3V,|      |
|    |    |         |              |              |SOIC14                       |      |
|47  |1   |U200     |SN74AHCT1G125_|              |Single TTL Buffer, SC-70-5   |      |
|    |    |         |DCK           |              |                             |      |
|48  |1   |S100     |SW_SPST_SWT6-E|              |Tactile Pushbutton, SPST, 6mm|      |
|    |    |         |5M            |              |                             |      |
|49  |1   |U301     |TPS5401       |              |Integrated Buck Converter,   |      |
|    |    |         |              |              |0.5A Max, 42V In Max         |      |
|50  |1   |U302     |TPS79333      |              |3.3V LDO, 200mA Maximum      |      |
|    |    |         |              |              |current                      |      |
|51  |7   |D200-204 |TVS_NUP2105LT1|              |Dual Bidirectional TVS Diode,|      |
|    |    |D400-401 |G             |              |350W, SOT-23                 |      |
|--------------------------------------------------------------------------------------|

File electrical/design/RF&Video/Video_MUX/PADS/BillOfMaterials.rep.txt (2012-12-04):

|-----------------------------------------------------------------------|
|Bill Of Materials for videoMux.sch on Tue Nov 27 16:26:55 2012         |
|-----------------------------------------------------------------------|
|Item|Qty |Reference|Part Name     |Description                  |Value |
|----+----+---------+--------------+-----------------------------+------|
|1   |6   |J1-4 J6-7|142146-75     |SMB, Right Angle             |      |
|2   |1   |Y1       |ABM2-16.000MHZ|Crystal                      |      |
|    |    |         |-D4Y-T        |                             |      |
|3   |1   |U33      |ATXMEGA128A3  |MCU, 8/16b,AVR,              |      |
|    |    |         |              |ATXMega128A3AU               |      |
|4   |1   |D28      |B2100-13      |High Voltage Schottky Diode  |      |
|5   |45  |D2-12    |B72500D0050A06|Bidirectional TVS Diode      |      |
|    |    |D14-15   |0             |                             |      |
|    |    |D18      |              |                             |      |
|    |    |D20-27   |              |                             |      |
|    |    |D29-51   |              |                             |      |
|6   |1   |D1       |BAS40         |Schottky Diode               |      |
|7   |1   |C34      |CAP-0402,     |Capacitor                    |1000pF|
|    |    |         |1000pF,2%     |                             |      |
|8   |1   |C39      |CAP-0402,     |Capacitor                    |1500pF|
|    |    |         |1500pF,5%     |                             |      |
|9   |1   |C35      |CAP-0402,     |Capacitor                    |360pF |
|    |    |         |360pF,5%      |                             |      |
|10  |1   |C40      |CAP-0402,     |Capacitor                    |620pF |
|    |    |         |620pF,5%      |                             |      |
|11  |1   |C36      |CAP-0402,     |Capacitor                    |680pF |
|    |    |         |680pF,2%      |                             |      |
|12  |40  |C1-16    |CAP-0603,     |Capacitor                    |0.1uF |
|    |    |C18-22   |0.1uF,10%     |                             |      |
|    |    |C24-25   |              |                             |      |
|    |    |C28-30   |              |                             |      |
|    |    |C33      |              |                             |      |
|    |    |C37-38   |              |                             |      |
|    |    |C42-48   |              |                             |      |
|    |    |C52 C105 |              |                             |      |
|    |    |C111 C116|              |                             |      |
|13  |2   |C103 C109|CAP-0603,10nF,|Capacitor                    |10nF  |
|    |    |         |5%            |                             |      |
|14  |1   |C100     |CAP-0603,     |Capacitor                    |2.2nF |
|    |    |         |2.2nF,5%      |                             |      |
|15  |3   |C49-51   |CAP-0603,27pF,|Capacitor                    |27pF  |
|    |    |         |5%            |                             |      |
|16  |2   |C17 C23  |CAP-0805,10uF,|Capacitor                    |10uF  |
|    |    |         |10%           |                             |      |
|17  |4   |C26-27   |CAP-0805,1uF, |Capacitor                    |1uF   |
|    |    |C31-32   |10%           |                             |      |
|18  |7   |C53-54   |CAP-1206,10uF,|Capacitor                    |10uF  |
|    |    |C98-99   |10%           |                             |      |
|    |    |C104 C110|              |                             |      |
|    |    |C113     |              |                             |      |
|19  |1   |C102     |CAP-2917,     |Capacitor                    |220uF |
|    |    |         |220uF,10%     |                             |      |
|20  |1   |C41      |CAP-RADIAL-6.3|Radial Electrolytic          |100uF |
|    |    |         |X7_2.5MMP,    |Capacitor, 6.3x7x2.5mm       |      |
|    |    |         |100uF         |(DxHxP)                      |      |
|21  |1   |U1       |CD4051BM      |8:1 Analog Multiplexer       |      |
|22  |12  |J5 J8-12 |COAX_PAD      |Coaxial Test Point           |      |
|    |    |J20-21   |              |                             |      |
|    |    |J26      |              |                             |      |
|    |    |J29-31   |              |                             |      |
|23  |5   |J15      |HDR_2P1R_100MI|Standard 2 Pin 1 Row .100"   |      |
|    |    |J17-18   |L             |Header                       |      |
|    |    |J24-25   |              |                             |      |
|24  |4   |J13 J19  |HDR_3P1R_100MI|Header, 3P1R, 100mil         |      |
|    |    |J32-33   |L             |                             |      |
|25  |2   |J14 J27  |HDR_8P1R_100MI|Header, 8P1R, 100mil         |      |
|    |    |         |L             |                             |      |
|26  |1   |J22      |HDR_MINIFITJR_|Minifit Jr Header, 2P 2R     |      |
|    |    |         |2R2P-RA       |Right Angle                  |      |
|27  |1   |J28      |HDR_PDI_6     |Header, 6P 2 Row, Through    |      |
|    |    |         |              |Hole, Shroded, 100x100mil,   |      |
|    |    |         |              |for ISP-6 Programming        |      |
|28  |2   |J16 J23  |HDR_SHERLOCK_3|Molex Sherlock 2.0mm         |      |
|    |    |         |P_V           |Header-3P Vertical           |      |
|29  |1   |J204     |HDR_SHERLOCK_5|Molex Sherlock 2.0mm         |      |
|    |    |         |P_V           |Header-5P Vertical           |      |
|30  |4   |X1-4     |HOLE_4-40     |Hole for 4-40 screw          |      |
|31  |1   |U15      |INA134        |Balanced Audio Receiver      |      |
|32  |1   |L2       |IND0402,1.2uH,|Inductor                     |1.2uH |
|    |    |         |10%           |                             |      |
|33  |1   |L1       |IND0402,1.5uH,|Inductor                     |1.5uH |
|    |    |         |10%           |                             |      |
|34  |1   |D19      |LED-0805_DIALI|LED, 0805, Yellow            |      |
|    |    |         |GHT_598-8150-1|                             |      |
|    |    |         |07F           |                             |      |
|35  |2   |D13 D17  |LED-0805_DIALI|LED                          |      |
|    |    |         |GHT_598-8170-1|                             |      |
|    |    |         |07F           |                             |      |
|36  |1   |U13      |LM4040A30I    |Voltage Reference            |      |
|37  |1   |U29      |LT1054CDW     |Charge Pump                  |      |
|38  |2   |U2 U9    |MAX864        |Dual Charge Pump             |      |
|39  |1   |U10      |MCP4011,2.1K  |64 step digital              |2.1K  |
|    |    |         |              |potentiometer, 4MHz -3dB     |      |
|    |    |         |              |bandwidth                    |      |
|40  |6   |U3-7 U14 |OPA693        |Fixed Gain Video Buffer      |      |
|41  |1   |U32      |REG103GA-5    |LDO Voltage Regulator        |      |
|42  |1   |U31      |REG103GA-3.3  |LDO Voltage Regulator        |      |
|43  |1   |R107     |RES-0603,102K,|Resistor                     |102K  |
|    |    |         |1%            |                             |      |
|44  |2   |R109 R116|RES-0603,150, |Resistor                     |150   |
|    |    |         |1%            |                             |      |
|45  |1   |R22      |RES-0603,200K,|Resistor                     |200K  |
|    |    |         |5%            |                             |      |
|46  |1   |R106     |RES-0603,20K, |Resistor                     |20K   |
|    |    |         |1%            |                             |      |
|47  |1   |R18      |RES-0603,2K,5%|Resistor                     |2K    |
|48  |1   |R98      |RES-0603,300, |Resistor                     |300   |
|    |    |         |1%            |                             |      |
|49  |1   |R115     |RES-0603,324, |Resistor                     |324   |
|    |    |         |1%            |                             |      |
|50  |11  |R26 R28  |RES-0603,4.7K,|Resistor                     |4.7K  |
|    |    |R38      |5%            |                             |      |
|    |    |R41-43   |              |                             |      |
|    |    |R48-49   |              |                             |      |
|    |    |R119-121 |              |                             |      |
|51  |9   |R11-15   |RES-0603,75,1%|Resistor                     |75    |
|    |    |R19 R23  |              |                             |      |
|    |    |R25 R27  |              |                             |      |
|52  |6   |R20-21   |RES-0603,???  |Resistor                     |???   |
|    |    |R34-35   |              |                             |      |
|    |    |R100 R102|              |                             |      |
|53  |26  |R1-10    |RES-0603,OPT-0|Resistor                     |OPT-0 |
|    |    |R16-17   |              |                             |      |
|    |    |R24      |              |                             |      |
|    |    |R29-33   |              |                             |      |
|    |    |R36-37   |              |                             |      |
|    |    |R39-40   |              |                             |      |
|    |    |R45-47   |              |                             |      |
|    |    |R108     |              |                             |      |
|54  |1   |R44      |RES-0603,     |Resistor                     |OPT-10|
|    |    |         |OPT-100       |                             |0     |
|55  |1   |U35      |SN65HVD35     |RS-485 Transceiver           |      |
|56  |1   |SW1      |SW_SKHHAMA010 |Tactile Push-button          |      |
|57  |2   |U8 U12   |THS4011CD     |High Frequency OP-AMP        |      |
|58  |1   |U11      |TLC548CD      |Single Channel ADC           |      |
|59  |6   |TPNT1-6  |TPNT          |Test point with via          |      |
|-----------------------------------------------------------------------|

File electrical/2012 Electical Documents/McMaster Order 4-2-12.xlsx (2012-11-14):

Description | Part No. | QTY | Cost / Unit | Cost @ QTY | Total Cost
Solder, 60:40, Rosin Core, 1lb | 7659A5 | 1 | $30.98 | $30.98 | 146.81
Flux Pen | 7893A22 | 1 | $7.76 | $7.76
Expandable Cable Sleeving, 1/8in, 10ft | 9284K411 | 2 | $2.52 | $5.04
Expandable Cable Sleeving, 1/4in, 10ft | 9284K412 | 2 | $2.65 | $5.30
Expandable Cable Sleeving, 1/2in, 10ft | 9284K414 | 3 | $5.30 | $15.90
Heat Shrink Tubing Assortment | 6334K41 | 1 | $67.65 | $67.65
Ring Terminal, 16-14AWG, 1/4in, 10 | 7113K255 | 1 | $3.09 | $3.09
Ring Terminal, 16-14AWG, 3/8in, 10 | 7113K951 | 1 | $4.95 | $4.95
Ring Terminal, 16-12AWG, 1/2in, 10 | 9388K38 | 1 | $6.14 | $6.14

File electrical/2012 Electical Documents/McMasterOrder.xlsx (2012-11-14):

Part # | Description | Cost / Unit | Quantity | Total Cost | Grand Total
6949K62 | Grounding Braid | 2.48 | 5 | $12.40 | 100.3
90279A108 | 3/8" 4-40 Screw | 4.21 | 400 | 16.84
71245K41 | 12AWG MTW BLK | 24.39 | 50 | 12.195
71245K44 | 12AWG MTW RED | 24.39 | 50 | 12.195
71245K21 | 16AWG MTW BLK | 13.48 | 50 | 6.74
71245K24 | 16AWG MTW RED | 13.48 | 50 | 6.74
71245K23 | 16AWG MTW YEL | 13.48 | 50 | 6.74
71245K11 | 18AWG MTW BLK | 10.58 | 50 | 5.29
71245K16 | 18AWG MTW BLU | 10.58 | 50 | 5.29
71245K101 | 18AWG MTW ORG | 10.58 | 50 | 5.29
71245K12 | 18AWG MTW WHT | 10.58 | 50 | 5.29
71245K102 | 18AWG MTW BRN | 10.58 | 50 | 5.29

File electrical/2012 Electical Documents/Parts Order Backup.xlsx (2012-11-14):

 |  |  |  | MUX | CPC | MTRCTL | ARMBS | WRST | ZGB | TPD | RFFE | SLD | OTHER | Sub System
 |  |  |  | 1 | 2 | 8 | 1 | 1 | 2 | 1 | 1 | 2 | 1 | Sub System QTY |  |  |  |  | Total Cost
Description | Link | Value | Part No. | Part QTY | Part QTY | Part QTY | Part QTY | Part QTY | Part QTY | Part QTY | Part QTY | Part QTY | Part QTY | Total Part QTY | Spares | QTY to Order | Cost / Part @ QTY | Cost @ QTY | 1853.6
16MHz Crystal | http://www.mouser.com/ProductDetail/ABRACON/ABM2-16000MHZ-D4Y-T/?qs=exgkNhLRQG%252bA17mYO7cVJQ%3d%3d | 16MHz | ABM2-16.000MHZ-D4Y-T | 1 | 1 | 1 |  |  |  |  |  |  |  | 11 | 3 | 14 | 0.58 | 8.12
8bit Microcontroller | http://components.arrow.com/part/detail/51486188S9135531N3744 |  | ATXMEGA192-A3-AU | 1 | 1 |  |  | 1 |  | 1 | 1 |  |  | 6 | 3 | 9 | 5.74 | 51.66
8bit Microcontroller | http://components.arrow.com/part/detail/47542273S8447338N3744 |  | ATXMEGA32D4 |  |  | 1 |  |  |  |  |  |  |  | 8 | 4 | 12 | 3.15 | 37.8
High Voltage Schottky Diode | http://www.mouser.com/ProductDetail/Diodes-Inc/B2100-13-F/ |  | B2100-13 | 1 |  |  |  |  |  |  |  |  |  | 1 | 1 | 2 | 0.58 | 1.16
Bidirectional TVS Diode | http://www.mouser.com/ProductDetail/EPCOS/B72500D0050A060/?qs=pGJ4H8VyKtVj2stqo73RQQ%3d%3d |  | B72500D0050A060 | 45 |  |  |  |  |  |  |  |  |  | 45 | 13 | 58 | 0.14 | 8.12
Schottky Diode | http://www.mouser.com/Search/ProductDetail.aspx |  | BAS40-05-V-GS08 | 1 |  |  |  |  |  |  |  |  |  | 1 | 1 | 2 | 0.09 | 0.18
Capacitor, 0402 | http://www.mouser.com/ProductDetail/Murata/GRM1555C1H102GA01D/?qs=pwh76yelNxBq2Xo4ufc5bQ%3d%3d | 1000pF | GRM1555C1H102GA01D | 1 |  |  |  |  |  |  |  |  |  | 1 | 1 | 2 | 0.09 | 0.18
Capacitor, 0402 | http://www.mouser.com/ProductDetail/Murata/GRM155R71H152JA01D/ | 1500pF | GRM155R71H152JA01D | 1 |  |  |  |  |  |  |  |  |  | 1 | 1 | 2 | 0.09 | 0.18
Capacitor, 0402 | http://www.mouser.com/ProductDetail/Murata/GRM1555C1H361JA01D/?qs=xcCo%252bfWZmQUhWvj8kQFSHg%3d%3d | 360pF | GRM1555C1H361JA01D | 1 |  |  |  |  |  |  |  |  |  | 1 | 1 | 2 | 0.09 | 0.18
Capacitor, 0402 | http://www.mouser.com/ProductDetail/Murata/GRM1555C1E621JA01D/?qs=MY6wChARw2yw2GwkA8mCsA%3d%3d | 620pF | GRM1555C1E621JA01D | 1 |  |  |  |  |  |  |  |  |  | 1 | 1 | 2 | 0.09 | 0.18
Capacitor, 0402 | http://www.mouser.com/ProductDetail/Murata/GRM1555C1H681GA01D/?qs=pwh76yelNxBMHV6o85e5HQ%3d%3d | 680pF | GRM1555C1H681GA01D | 1 |  |  |  |  |  |  |  |  |  | 1 | 1 | 2 | 0.09 | 0.18
Capacitor, 0603 | http://www.mouser.com/ProductDetail/Murata/GRM188R71H104KA93J/?qs=f7ZljCwbPOkOphVK4w%2fceQ%3d%3d | 0.1uF | GRM188R71H104KA93J | 40 | 21 | 13 |  |  | 5 |  |  |  |  | 196 | 58 | 254 | 0.03 | 7.62
Capacitor, 0603 | http://www.mouser.com/Search/ProductDetail.aspx | 10nF | C0603C103J4RACTU | 2 |  | 2 |  |  |  |  |  |  |  | 18 | 5 | 23 | 0.1 | 2.3
Capacitor, 0603 | https://www.mouser.com/Search/ProductDetail.aspx | 2.2nF | C0603C222J5RACTU | 1 |  |  |  |  |  |  |  |  |  | 1 | 1 | 2 | 0.07 | 0.14
Capacitor, 0603 | https://www.mouser.com/Search/ProductDetail.aspx | 27pF | GRM1885C1H270JA01D | 3 |  |  |  |  |  |  |  |  |  | 3 | 2 | 5 | 0.1 | 0.5
Capacitor, 0603 | https://www.mouser.com/Search/ProductDetail.aspx | 10uF | GRM21BR61E106KA73L | 2 |  |  |  |  |  |  |  |  |  | 2 | 1 | 3 | 0.26 | 0.78
Capacitor, 0805 | http://www.mouser.com/ProductDetail/Murata/GCJ21BR71E105KA12L/?qs=TpyF2b7C1Q8QAAYag8J7gg%3d%3d | 1uF | GCJ21BR71E105KA12L | 4 |  |  |  |  |  |  |  |  |  | 4 | 2 | 6 | 0.2 | 1.2
Capacitor, 1206 | http://www.mouser.com/ProductDetail/Murata/GRM319R61E106KA12D/?qs=Uw8ySfEHS7I%2f0%252b02Z9D8CA%3d%3d | 10uF | GRM319R61E106KA12D | 7 | 1 |  |  |  |  |  |  |  |  | 9 | 5 | 14 | 0.36 | 5.04
Capacitor, 2917 | http://www.mouser.com/ProductDetail/Kemet/T491D227K016ZT/?qs=9ccv6DTEiZLNnpD9X6aekg%3d%3d | 220uF | T491D227K016ZT | 1 |  |  |  |  |  |  |  |  |  | 1 | 1 | 2 | 1.11 | 2.22
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

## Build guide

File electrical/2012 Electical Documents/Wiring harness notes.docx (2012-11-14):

- Out of red 16AWG MTW
- Out of black 16AWG MTW
- Low on black 18AWG MTW
- 16AWG MTW does not fit into LF-13 pins easily using 18AWG to support 32A instead of 44A
- Order more LF-13 11P BH connectors

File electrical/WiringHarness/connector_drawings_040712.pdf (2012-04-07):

# Full Duplex RS-485 Standard Connector

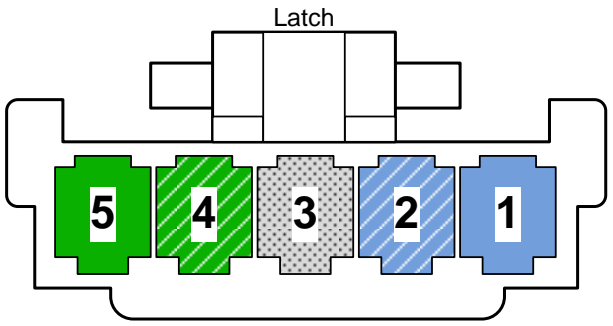
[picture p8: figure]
Latch

### Green Pair-Solid

### Green Pair-Striped

### Drain Wire/Shield

### Blue Pair-Striped

### Blue Pair-Solid

## Key

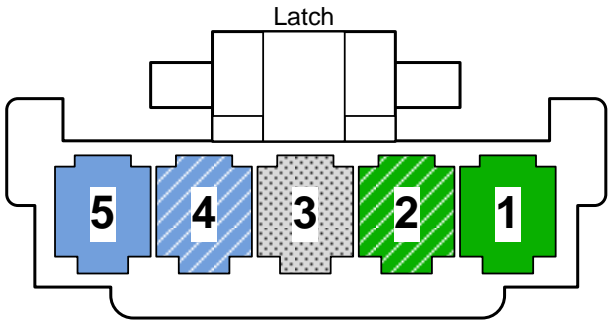
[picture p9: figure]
Latch

# Master Side (CPC)

# Slave Side (All Other Devices)

## Parameters

Cable Type: Cat5e, 4-Pair SSTP, 24AWG
Contacts: Sherlock Socket (Molex 50212-8000)
Connectors: Sherlock 5-Pin Wire Housing (Molex 35507-1500)

## Relevant Cables

Master Side: DAT-ARM,DAT-LBOG,DAT-BBOG,DAT- RBOG,DAT-INT,DAT-TRI

Slave Side: DAT-INT, DAT-BOGCTL(1-6),DAT-ARMBASE,DAT- WRIST,DAT-TRICTL

Rx+ | Rx- | GND | Tx- | Tx+

# Sherlock 5P Receptacle (Back)

# Sherlock 5P Receptacle (Back)

Rx+ | Rx- | GND | Tx- | Tx+

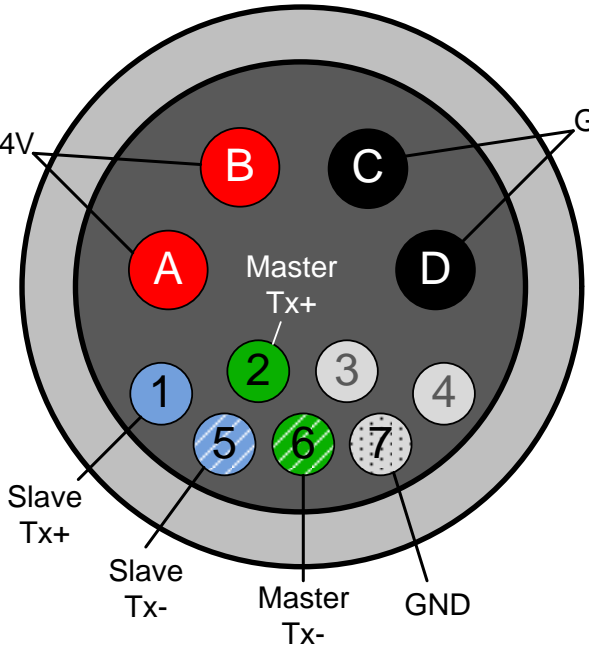
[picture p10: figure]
Master Tx+; Master; Tx- Slave Tx+; Slave; GND

## Parameters

Cable Type: Cat5e, 4-Pair SSTP, 24AWG, 16AWG Machine Tool Wire, 22AWG Shielded Audio Cable
Connectors: Hirose LF13-11(LF13WBR-11S and LF13WBP- 11P)

## Relevant Cables

DAT-LBOG,DAT-RBOG,DAT-BBOG,+24VDIST,GND, CMP- LBOG,CMP-RBOG,CMP-BBOG

+24V

### GND

# Bogie-Electrical Housing Connector

LF-13

# (Check Pin Designator)

## Key

### Blue Pair-Solid

### Blue Pair-Striped

### Drain Wire/Shield

### Green Pair-Striped

### Green Pair-Solid

### Red 16AWG

### Black 16AWG

### -Cat5e-

### -MTW-

### -Other- Unused

# Solenoid Driver Connectors

## Key

### Red 16AWG

### Black 16AWG

### -MTW-

### Blue 16AWG

1

3

2

4 | +24V SOL1
SOL2 | SOL3

# Solenoid Driver Output

# Minifit Jr. 4P2R Receptacle (Back)

1

3

2

4 | +24V

### GND

# Solenoid Driver Power

# Minifit Jr. 4P2R Receptacle (Back)

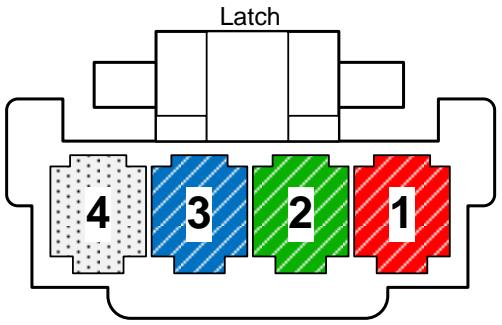
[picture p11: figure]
Latch

GND CTL3 CTL2 CTL3 | -4 Conductor- Green Wire
| Red Wire

### Blue Wire

# Sherlock 4P Receptacle (Back)

## Parameters

Cable Type: 16AWG Machine Tool Wire, 24AWG 4-Cond. Shielded Cable

Contacts: Sherlock Sockets (Molex 50212-8000), Molex Minifit Jr. Sockets
Connectors: Sherlock 4P Receptacle (Molex 35507-0400), Minifit Jr. 4P2R Receptacle

## Relevant Cables

PWR-SOL1, PWR-SOL2, DRV-SOL1, DRV-SOL2, CTL-SOL1, CTL-SOL2

### Drain Wire/Shield

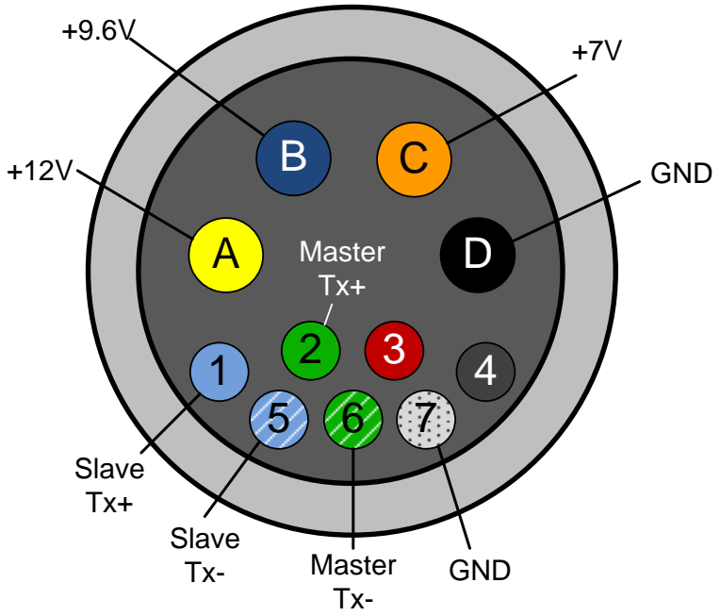
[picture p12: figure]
GND; Master Tx+; Master; Tx- Slave Tx+; Slave

## Parameters

Cable Type: Cat5e, 4-Pair SSTP, 24AWG, 16AWG Machine Tool Wire
Connectors: Hirose LF13-11(LF13WBR-11S and LF13WBP- 11P)

## Relevant Cables

DAT-TRI,CMP-TRI,+12V,+9.6V,+7V,GND

# Tripod-Electrical Housing Connector

LF-13

# (Check Pin Designator)

+7V | Key

### Blue Pair-Solid

### Blue Pair-Striped

### Drain Wire/Shield

### Green Pair-Striped

### Green Pair-Solid

### Orange 16AWG

### Black 16AWG

### -Cat5e-

### -MTW-

### -Audio Cable- Red Wire

### Black Wire

### Yellow 16AWG

### Blue 16AWG

# Arm-Electrical Housing Connectors

1

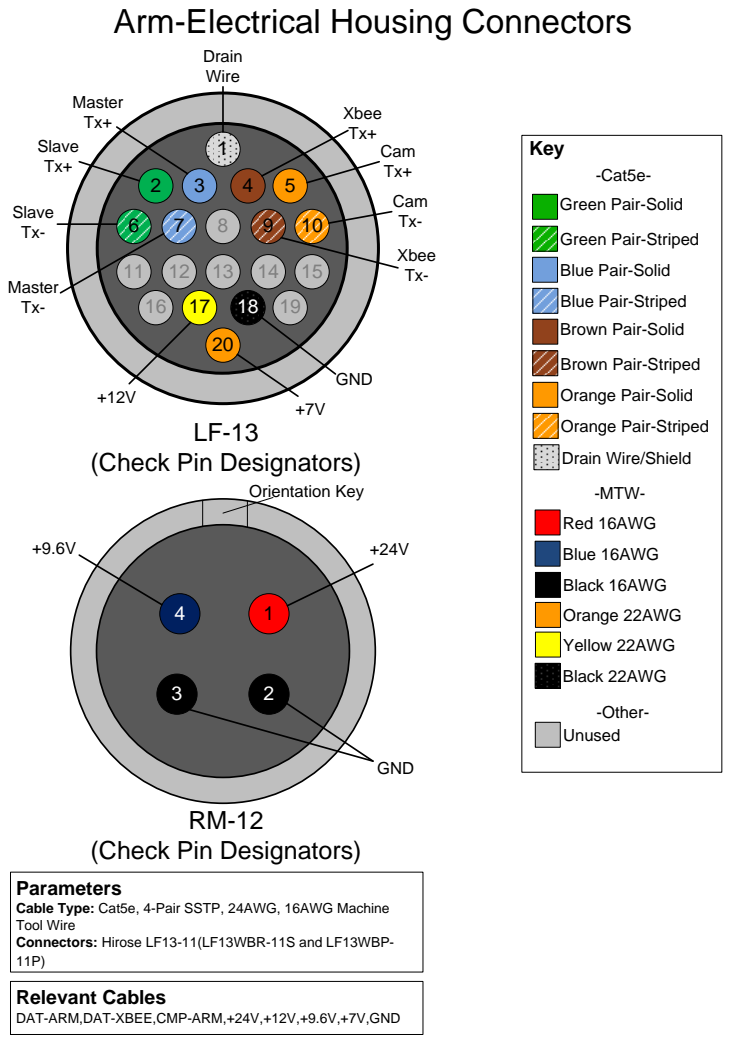
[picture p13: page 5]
-Other- Unused; Orange 22AWG; Black 16AWG; -MTW- Red 16AWG; Blue 16AWG; Yellow 22AWG; Black 22AWG; GND; Drain Wire; Slave Tx+; Slave Tx-; Master Tx+; Master Tx-; Cam Tx-; Cam Tx+; Xbee Tx+; Xbee Tx-; Orientation Key

Key
Green Pair-Solid -Cat5e-

Green Pair-Striped

Blue Pair-Solid

Blue Pair-Striped
Brown Pair-Solid

Brown Pair-Striped

Orange Pair-Solid

Orange Pair-Striped

(Check Pin Designators)

Drain Wire/Shield

Parameters
Cable Type: Cat5e, 4-Pair SSTP, 24AWG, 16AWG Machine
Tool Wire
Connectors: Hirose LF13-11(LF13WBR-11S and LF13WBP- 11P)

Relevant Cables
DAT-ARM,DAT-XBEE,CMP-ARM,+24V,+12V,+9.6V,+7V,GND

# XBee Interface Board I/O Connectors

3 | 2 | 1

# Sherlock 3P Receptacle (Back)

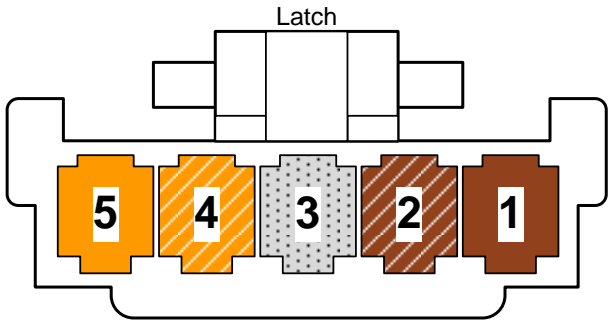
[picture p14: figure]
Latch

# Sherlock 5P Receptacle (Back)

### XBRx+ XBRx- GND XBTx- XBTx+

## Key

### Brown Pair-Solid

### Brown Pair-Striped

### Drain Wire/Shield

### Orange Pair-Striped

### Orange Pair-Solid

### -4 Conductor-

## Parameters

Cable Type: Cat5e 4-Pair SSTP 24AWG, 4 Conductor Shielded Cable
Contacts: Sherlock Receptacle (Molex 50212-8000) Connectors: Sherlock 3-Pin Wire Housing (Molex 35507-0300) , Sherlock 5-Pin Wire Housing (Molex 35507-1500)

## Relevant Cables

DAT-XBEE,CTL-XBEE

### GND SLEEP RESET

### Same on CPC Board Side

# XBee RS-485 Connector

# XBee Control Connector

### Blue Pair-Solid

### Green Pair-Solid

### Drain Wire/Shield -Cat5e-

# Freewave Connectors

10 | 9 | 8 | 7 6 | 5 | 4 | 3 | 2 1

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
# MTA-100 10P Connector (Top)

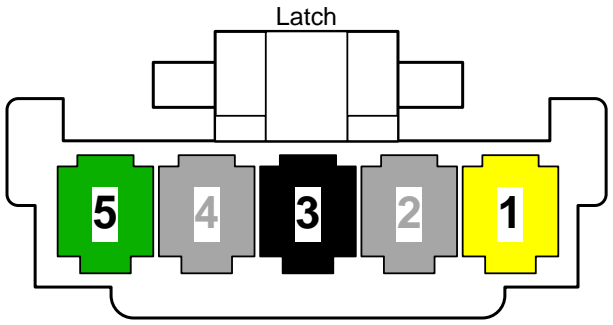
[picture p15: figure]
Latch

# Sherlock 5P Receptacle (Back)

Rx+ | N/A | GND N/A | Tx+

## Parameters

Cable Type: 10 wire Freewave Cable
Contacts: Sherlock Receptacle (Molex 50212-8000) Connectors: MTA-100 (Freewave Cable) , Sherlock 5-Pin Wire Housing (Molex 35507-1500), Minifit-Jr. 2- Pin Wire Housing

## Relevant Cables

DAT-FWV, PWR-FWV

1

2

# Minifit Jr. 2P2R Receptacle (Back) Freewave Power Connector

# Freewave Data Connector

# Freewave Main Connector

### GND

+12V | 1
2 | H
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
## Key

### FWV Black

### FWV Orange

### FWV Brown

### FWV Red

### -MTW- 16-18AWG-Yellow

### 16-18AWG-Black -Freewave Cable-

### -Freewave Cable- FWV Yellow

### FWV Green

### FWV Blue

### FWV Purple

### FWV Gray

3 | 2 | 1

# Sherlock 3P Receptacle (Back)

### AUD+ AUD- GND

3 | 2 | 1

# Sherlock 3P Receptacle (Back)

### GND AUD GND

# Differential Audio Input

# Single-Ended Audio Output

# MUX Audio Connectors

## Key

### Drain Wire/Shield -Audio Cable- Audio Cable - Red

### Audio Cable - Black

## Parameters

Cable Type: Shielded Audio Cable, 1 Pair 20-22AWG Red/ Black, 18AWG MTW
Contacts: Sherlock Sockets (Molex 50212-8000), Minifit Jr. Sockets

Connectors: Sherlock 3-Pin Wire Housing (Molex 35507-0300), Minifit Jr. 2P Plug

## Relevant Cables

AV-DIFFAU, AV-SEAU, PWR-MUX

1

2

# Minifit Jr. 2P2R Receptacle (Back) Mux Power

### GND

+12V

### 16-18AWG-Yellow -MTW- 16-18AWG-Black

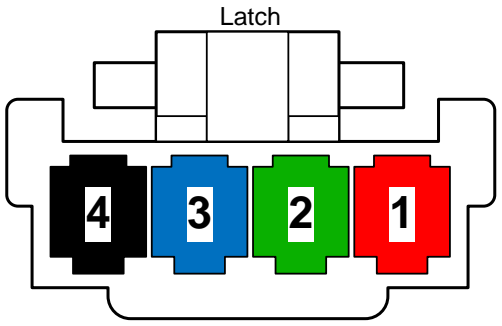
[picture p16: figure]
Latch

# Sherlock 4P Receptacle (Back)

GND | B | A | +5V

# Turn Motor Encoder Connector

# Bogie Controller I/O Connectors

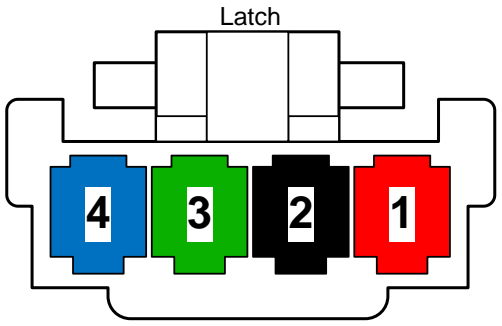
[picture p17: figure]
Latch

# Sherlock 4P Receptacle (Back)

B | A | GND | +5V

# Drive Motor Encoder Connector

# Power Input

# Power Output

### GND +24V

### V+ GND

## Parameters

Cable Type: 4 Conductor 24AWG Shielded, 16AWG MTW Contacts: Sherlock Sockets (Molex 50212-8000)
Connectors: Sherlock 4-Pin Wire Housing (Molex 35507-0400), Motor Interface Terminal Blocks

## Relevant Cables

SIG-TENC1-6, SIG-PENC1-6, DAT-MTRCTL1-12, PWR- MTRCTL1-6, PWR-MTRDRV1-6

## Key

### -4 Conductor- Red Wire

### Black Wire

### 16AWG-Red -MTW- 16AWG-Black

Tie

S

# hield

s to

G

r
o
u
n
d

### Green Wire

### Blue Wire

1

2

# Minifit Jr. 2P2R Receptacle (Back) CPC/XBee Power

+12V

### GND

### GND

+7V

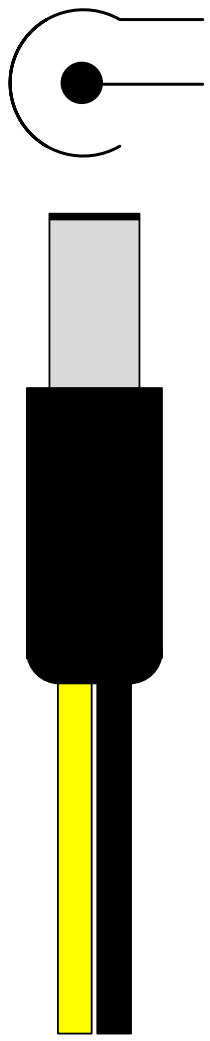
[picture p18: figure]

### +12V GND

# Miscellaneous Internal Power Connectors

## Parameters

Cable Type: 16-18AWG MTW
Contacts: Minifit Jr. Sockets
Connectors: Minifit Jr. 2P Plug, 2.1mm Barrel Plug

## Relevant Cables

PWR-CPC, PWR-FWV, PWR-VID

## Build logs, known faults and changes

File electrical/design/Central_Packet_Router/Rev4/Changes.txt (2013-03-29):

Changes Needed For Rev 4.
	-Serial Connector has to be rotated, it is backwards on the current Rev.
	-A linear regulator has to be added to power the Beagle Bone from the 
	 shield, the power will be coming from a 9 volt switching regulator
	-All Uarts will remain the same except the Int will become the gps
	 Uart and because of this the Tripod and Video Transmitter will be connected
	 to the full sized usb on the beagle bone and an usb hub will be used
	 to communicate with them
	-(?)Do we want to assign certain GPIO ports to the solenoids and place 
	 them specially on the board?
	-Board Silk Screen must be updated and MUST be included in the order this time
	-Add GPIO connectors for solenoids

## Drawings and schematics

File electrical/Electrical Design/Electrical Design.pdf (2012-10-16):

## Arm Motor System

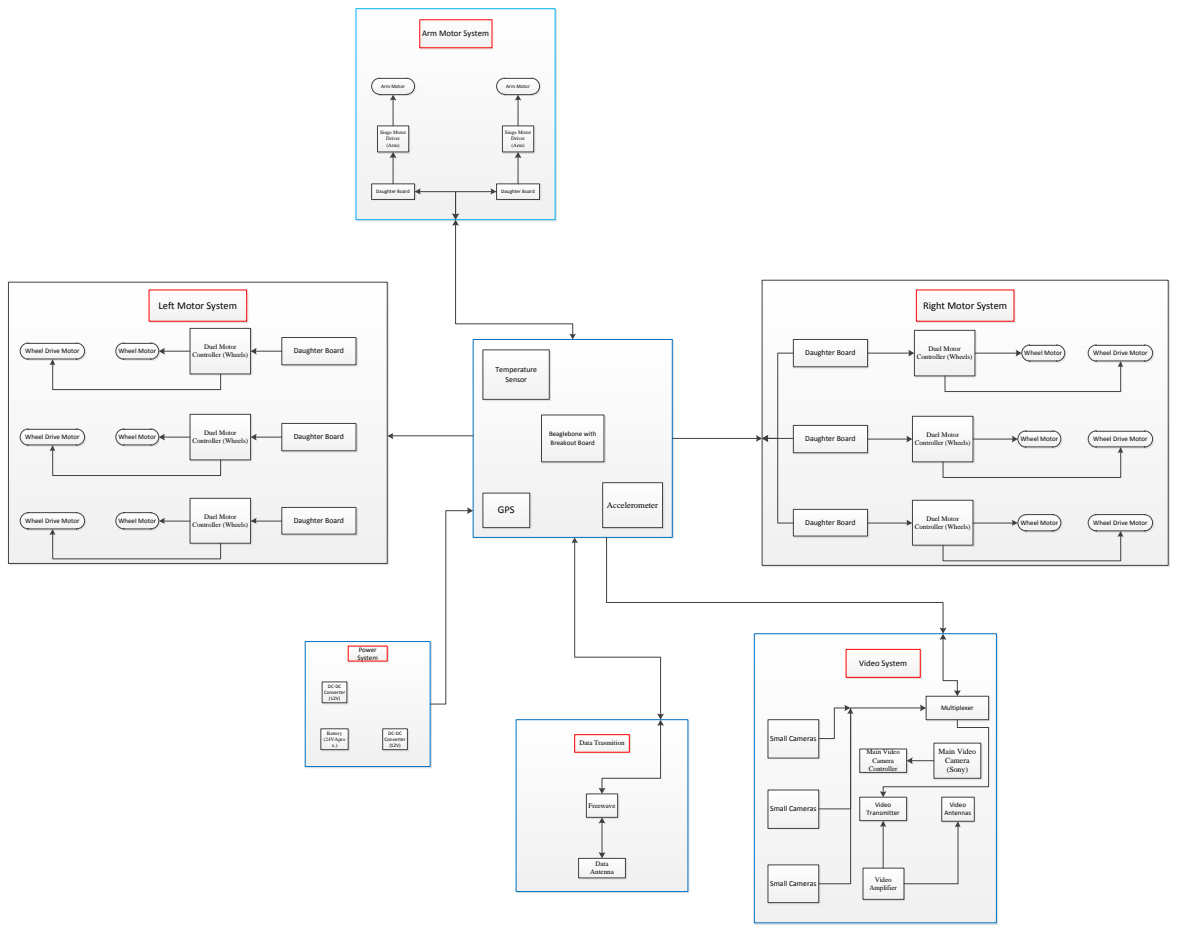
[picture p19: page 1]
GPS; Accelerometer; Temperature Sensor; Video System; Small Cameras; Video Amplifier; Power System; Battery (24VApro x.); DC-DC Converter (12V) DC-DC Converter (12V); Freewave; Data Trasmition; Data Antenna; Arm Motor; Daughter Board; Wheel Motor; Duel Motor Controller (Wheels); Left Motor System; Right Motor System; Multiplexer; Beaglebone with Breakout Board

Singe Motor Driver (Arm)

Duel Motor Controller (Wheels)

Wheel Drive Motor

Duel Motor Controller (Wheels) Wheel Motor

Main Video Camera (Sony)

Main Video Camera Controller

Video Antennas Video Transmitter

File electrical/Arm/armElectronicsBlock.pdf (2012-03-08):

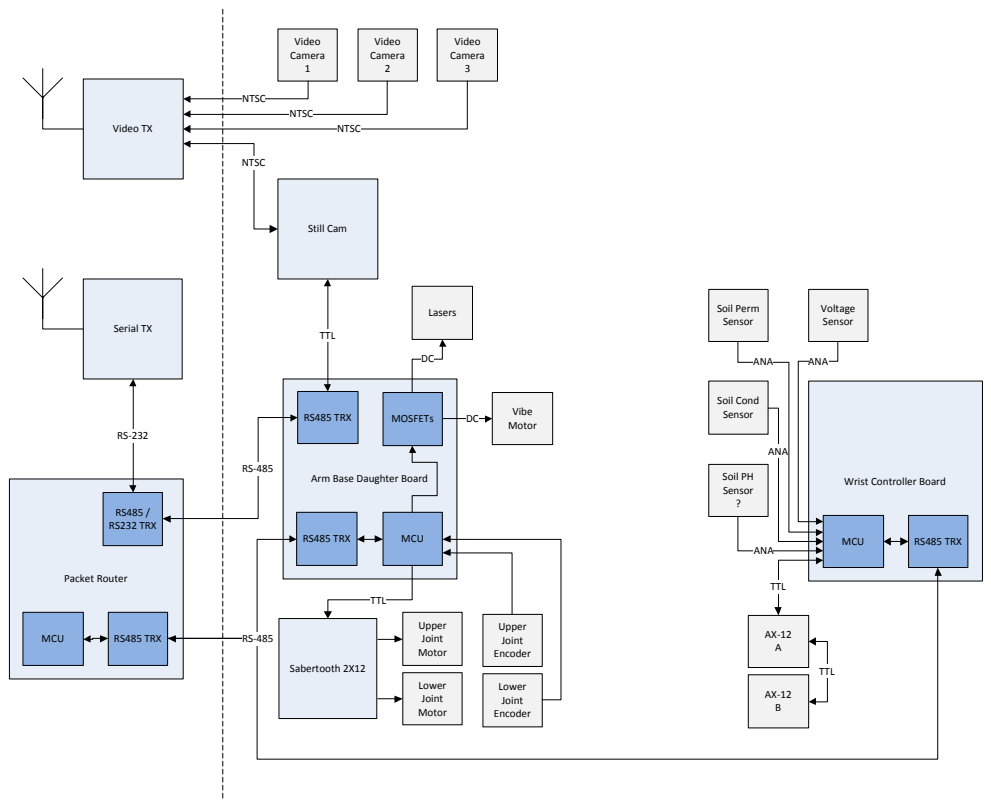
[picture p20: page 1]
Video TX; Serial TX; Packet Router; RS485 / RS232 TRX; MCU; RS485 TRX; Sabertooth 2X12; Lower Joint; Motor; Upper Joint; Encoder; Still Cam; TTL; NTSC; Soil Cond Sensor; Voltage Sensor; ANA; Soil PH Sensor ?; Video Camera 1; Video Camera 2; Video Camera 3; Vibe Motor MOSFETs; Lasers

Soil Perm Sensor

Arm Base Daughter Board

Wrist Controller Board

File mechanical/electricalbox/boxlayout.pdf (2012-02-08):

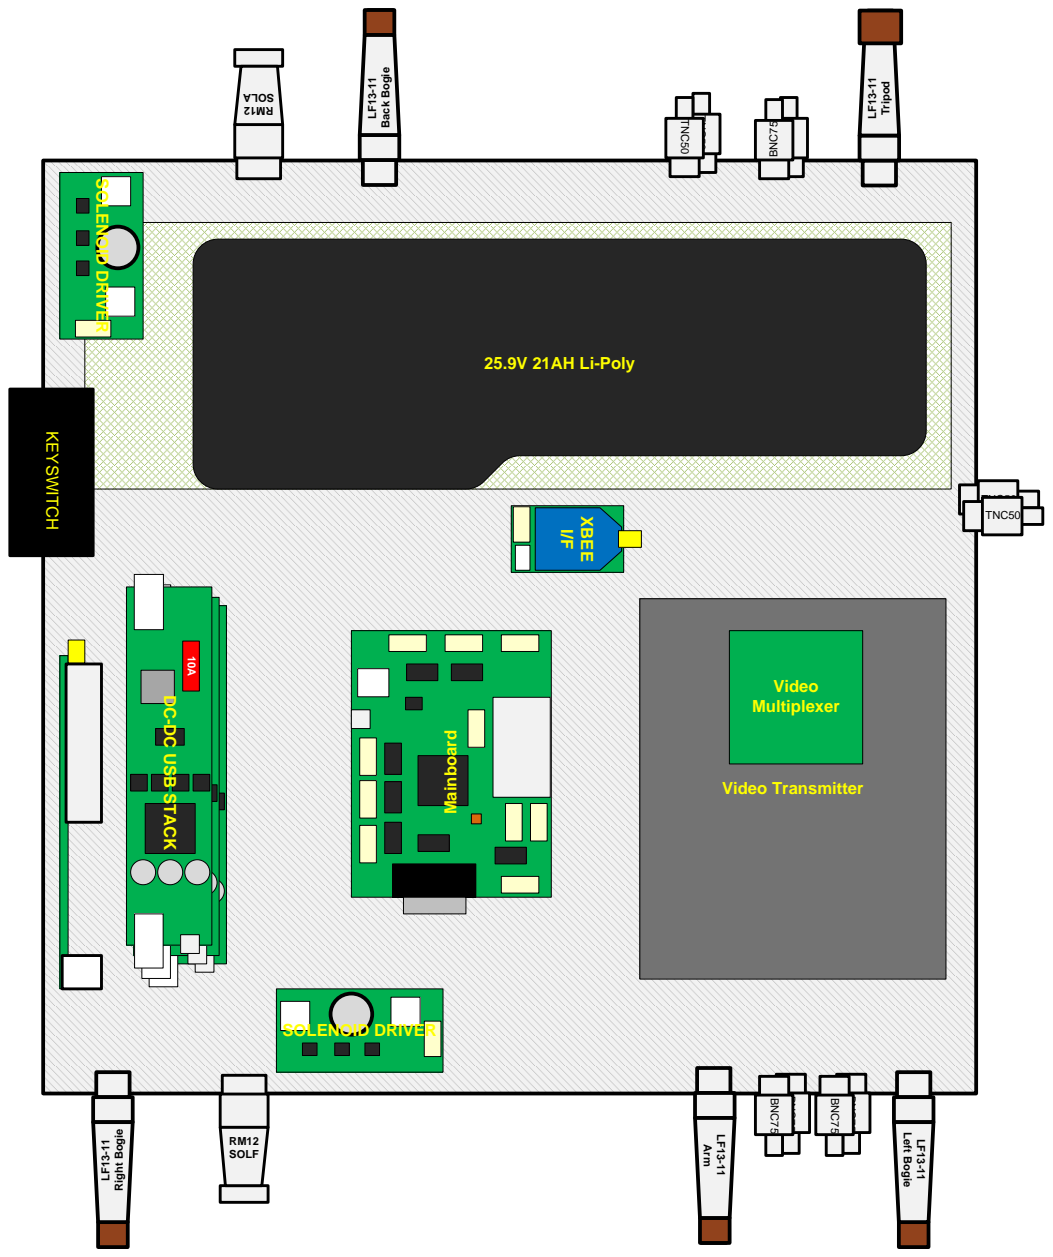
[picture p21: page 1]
ain; F13-11 L eft B; F13-11 Rig ht B; gie; F13-11 Trip; L F13-11 Arm; K E Y S WIT; TNC50; RM12 SOLF; Video Transmitter; Video Multiplexer; SOLENOID DRIVER; S O L E N OID; D RIV

Battery Area 25.9V 21AH Li-Poly

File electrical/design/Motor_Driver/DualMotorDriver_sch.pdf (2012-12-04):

D

6 | 5 | 4 | 3 | 2 | 1

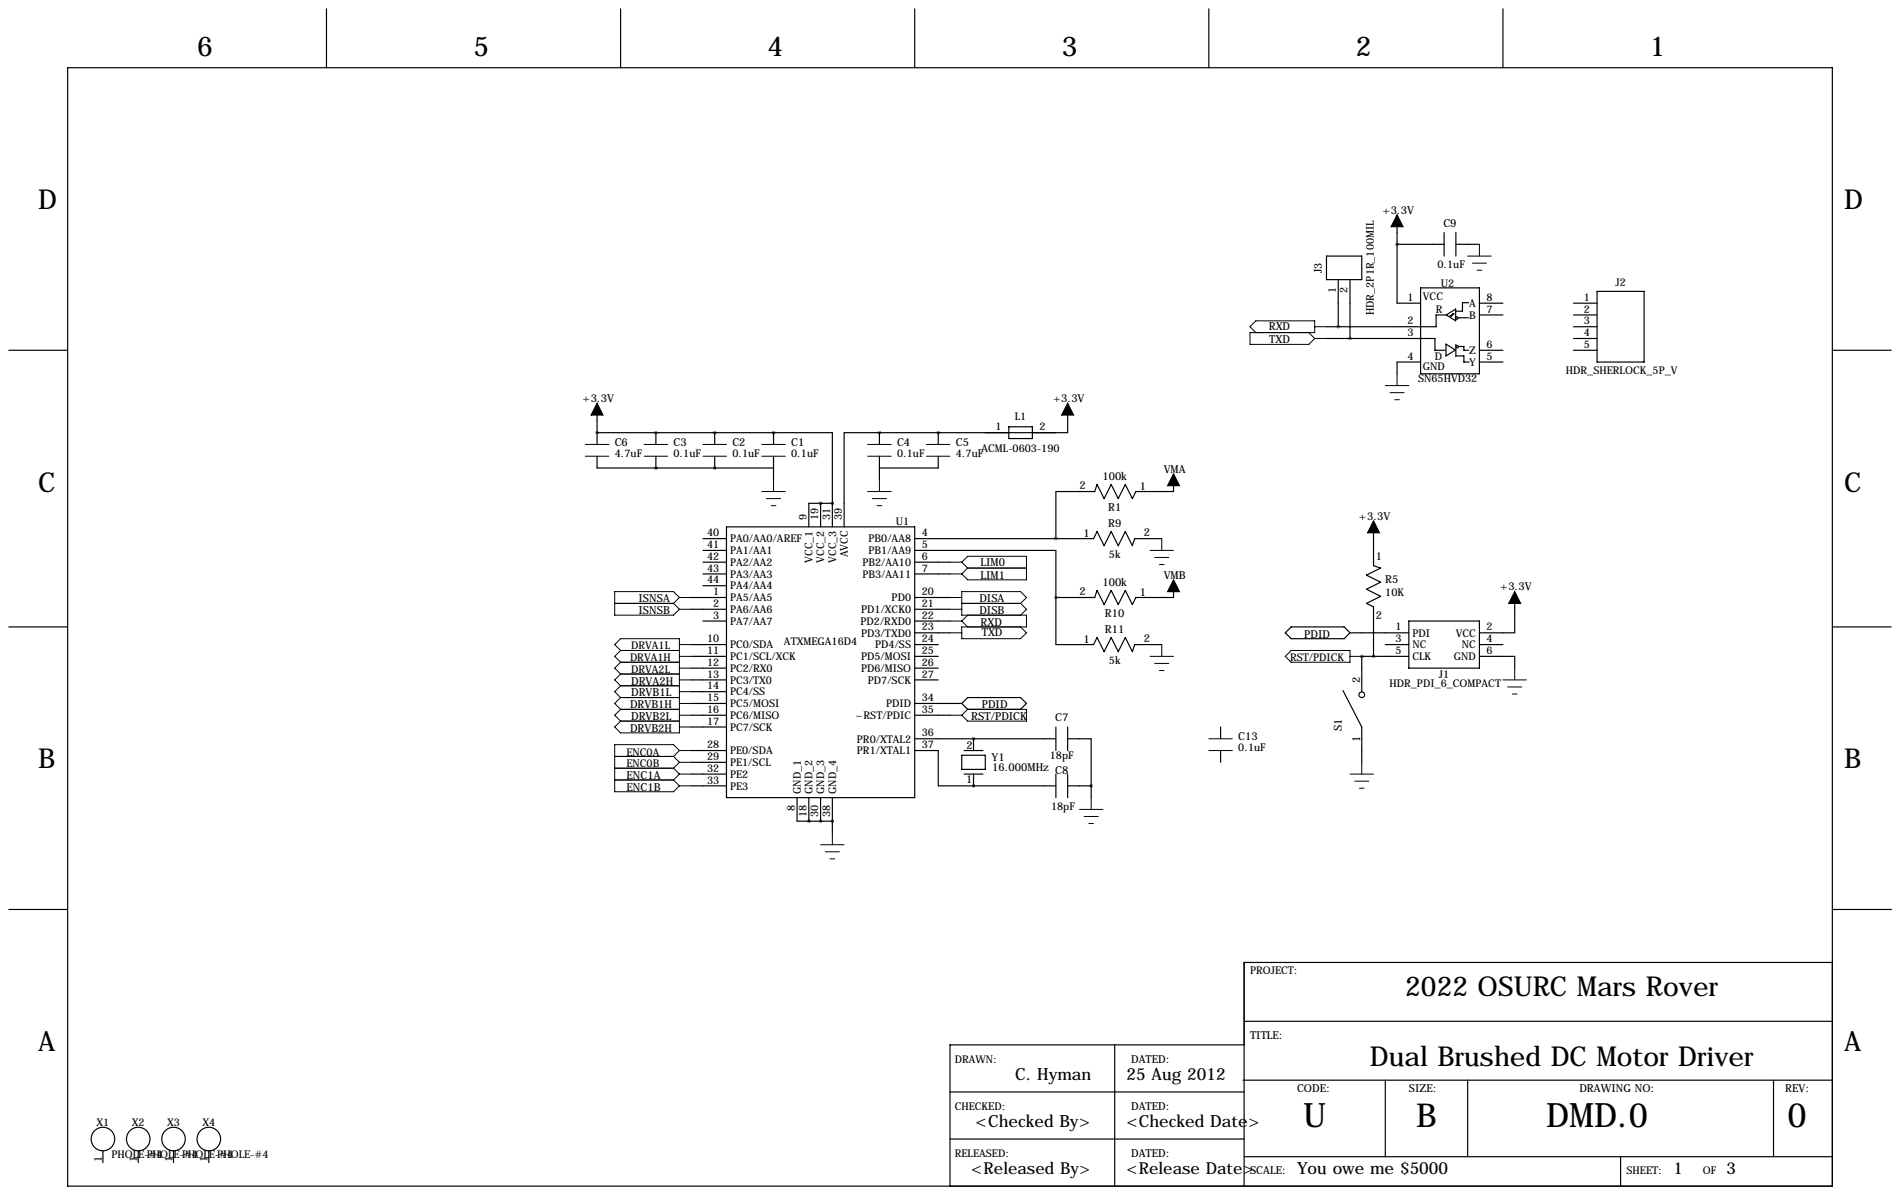
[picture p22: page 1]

DRAWN: C. Hyman | DATED: 25 Aug 2012

Dual Brushed DC Motor Driver

CODE: U | SIZE: B | DRAWING NO: DMD.0 | REV: 0

CHECKED: <Checked By> | DATED: <Checked Date>

RELEASED: <Released By> | DATED:

You owe me $5000 SCALE: | 1 3 SHEET: OF

D

D

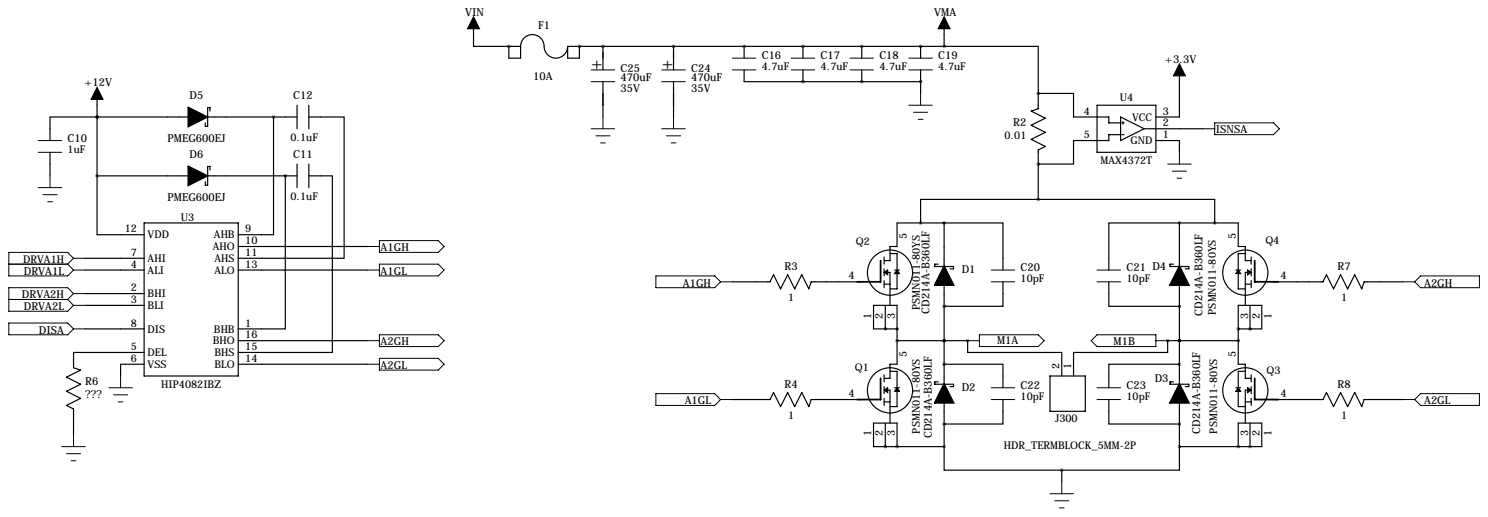
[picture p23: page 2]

D

D

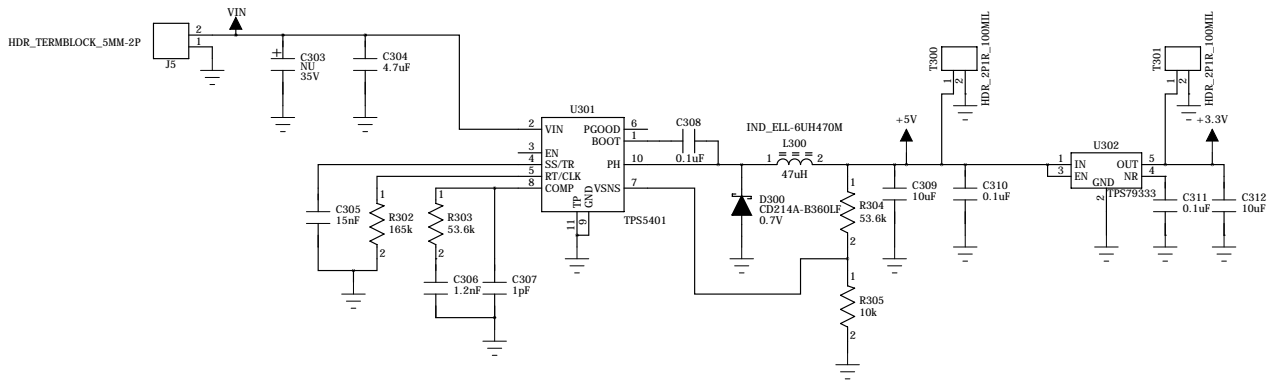
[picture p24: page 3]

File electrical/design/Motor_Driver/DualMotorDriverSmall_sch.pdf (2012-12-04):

D

6 | 5 | 4 | 3 | 2 | 1

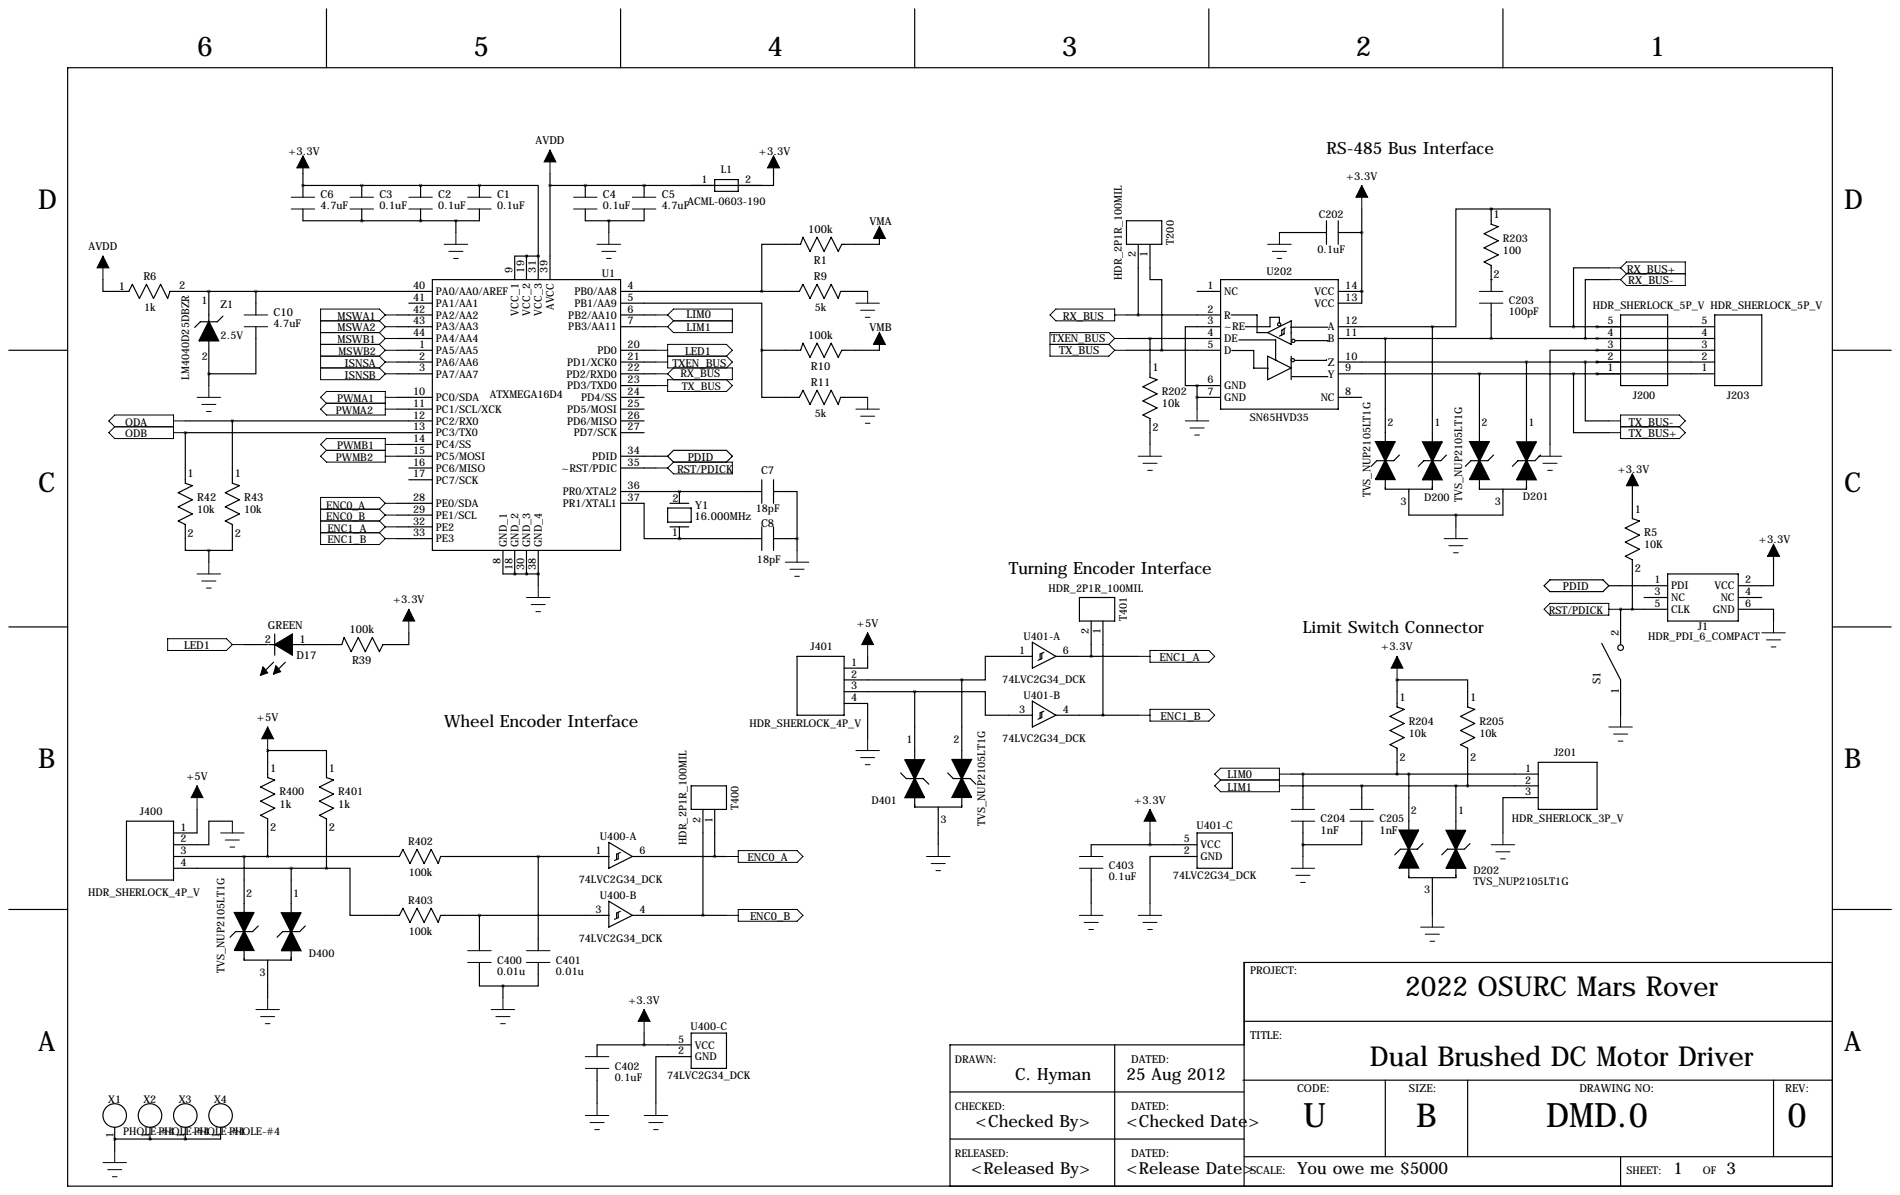
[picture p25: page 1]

Dual Brushed DC Motor Driver

CODE: U | SIZE: B | DRAWING NO: DMD.0 | REV: 0

CHECKED: <Checked By> | DATED: <Checked Date>

RELEASED: <Released By> | DATED:

You owe me $5000 SCALE: | 1 3 SHEET: OF

# BACD

6

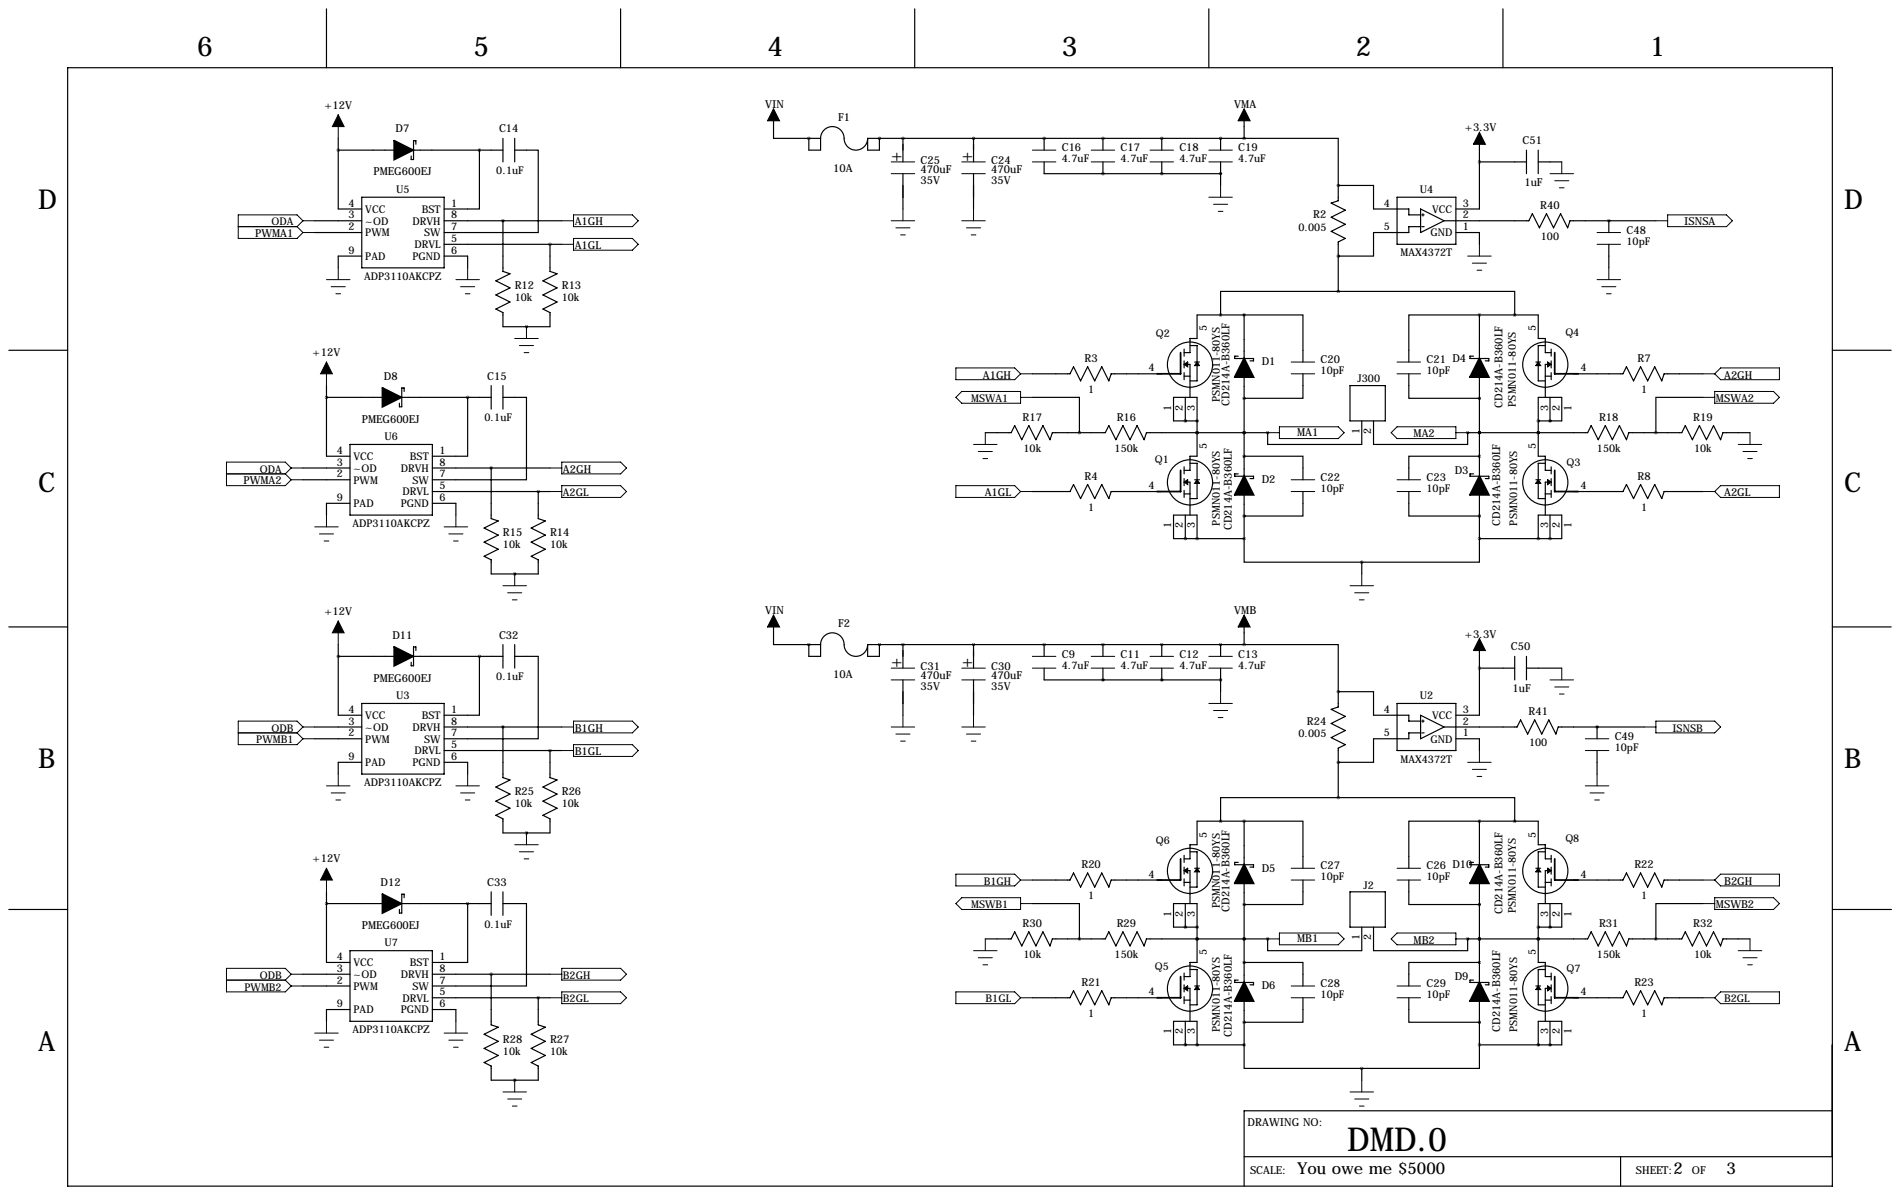
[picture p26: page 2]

SCALE: You owe me $5000

D

6 | 5 | 4 | 3 | 2 | 1

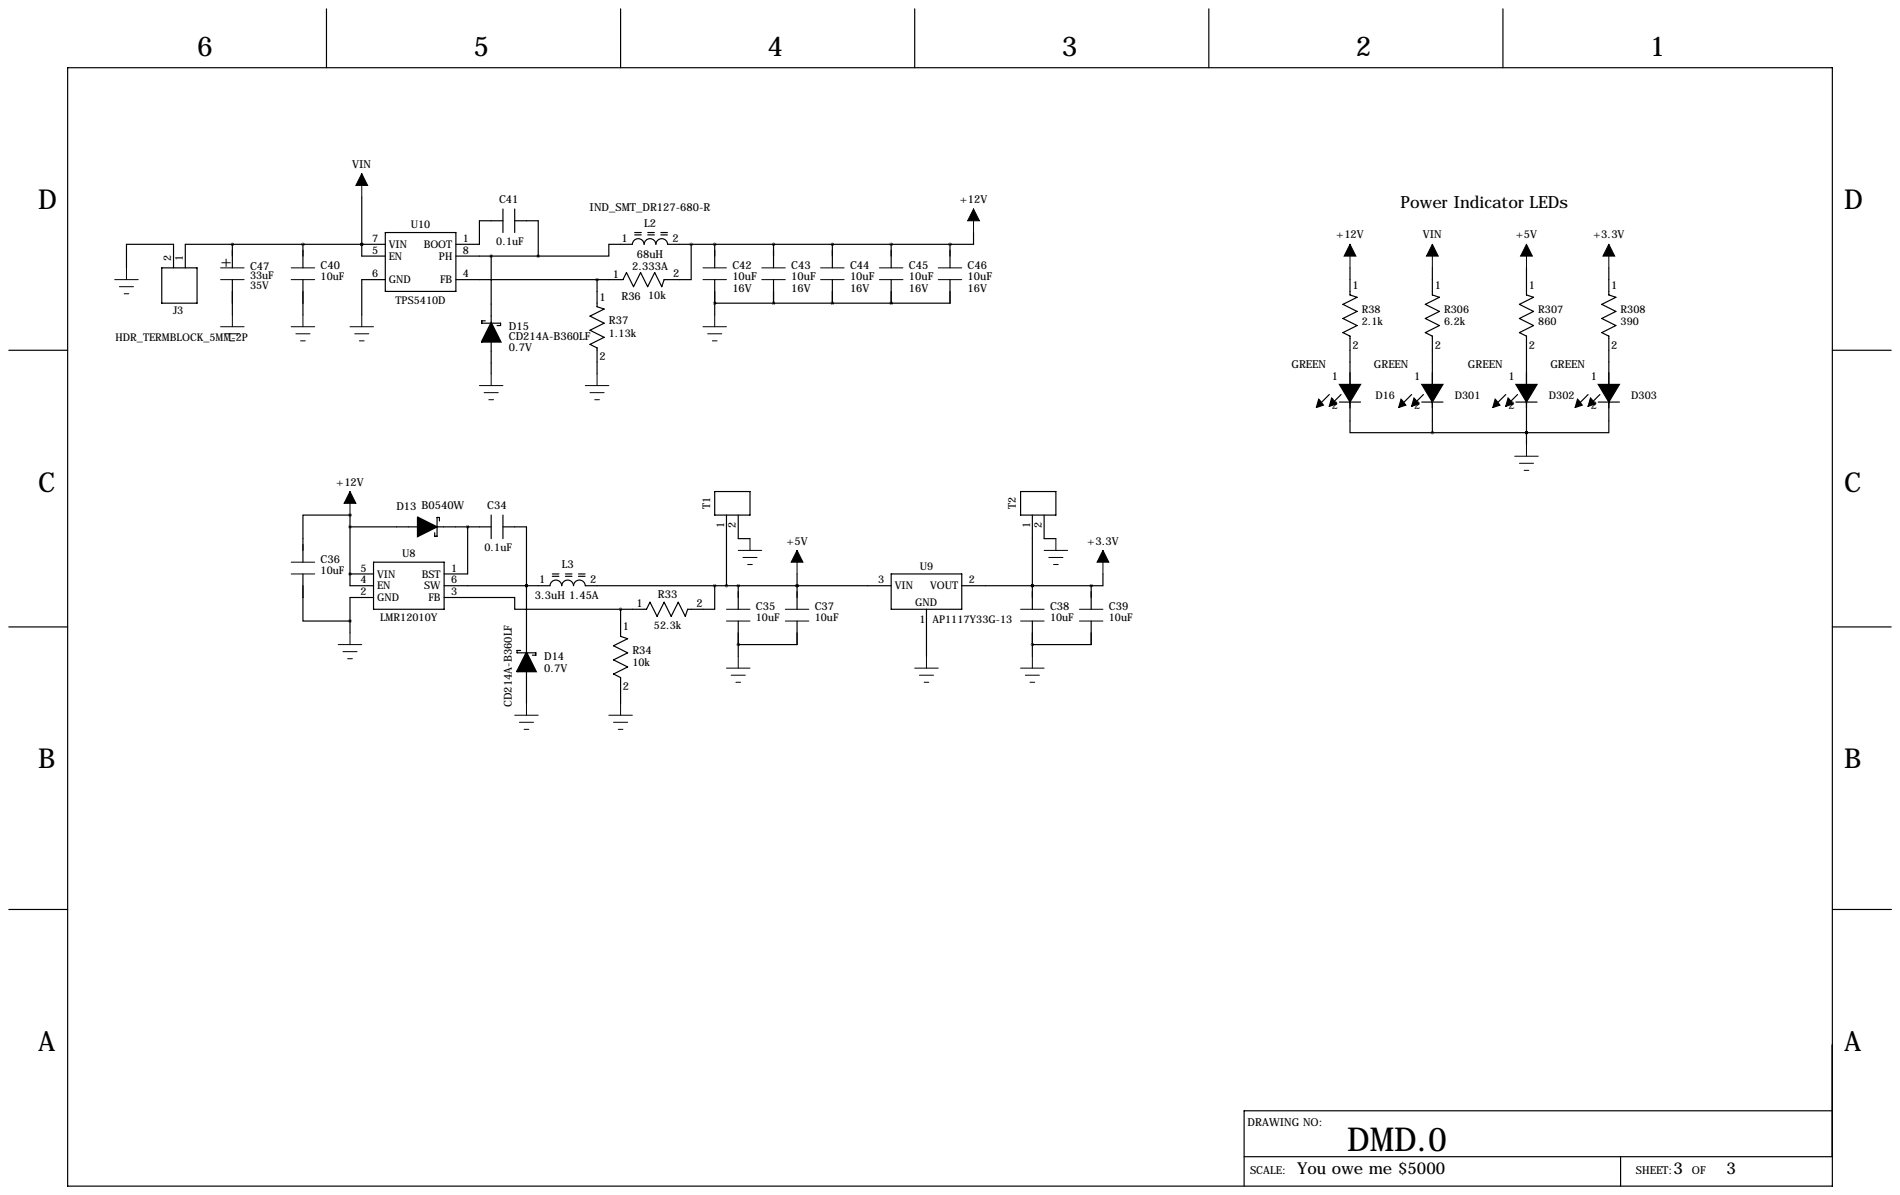
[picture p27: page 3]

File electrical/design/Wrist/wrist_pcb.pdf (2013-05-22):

# X2X²x1

# X4X⁴x1

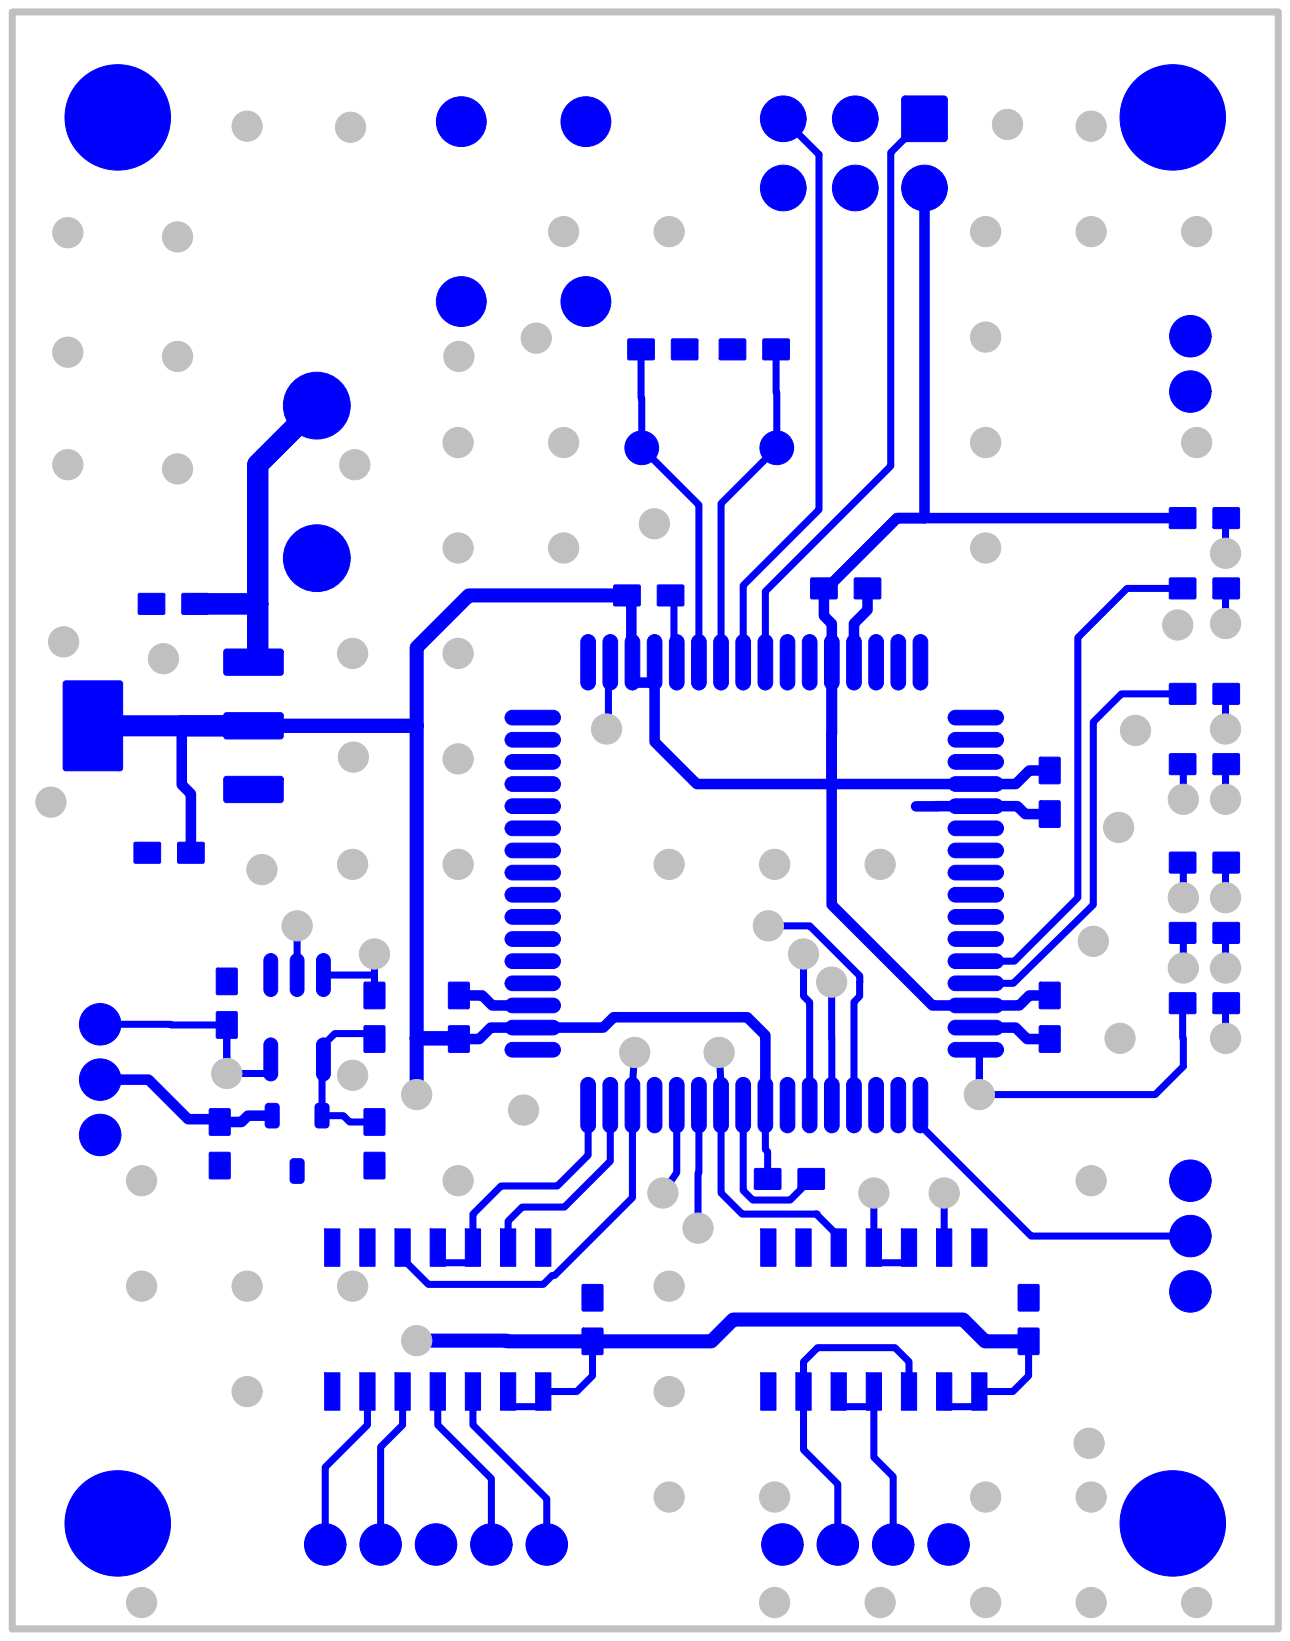
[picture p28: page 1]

# R103 R¹⁰³x2 R¹⁰³x1

# X2X²x1

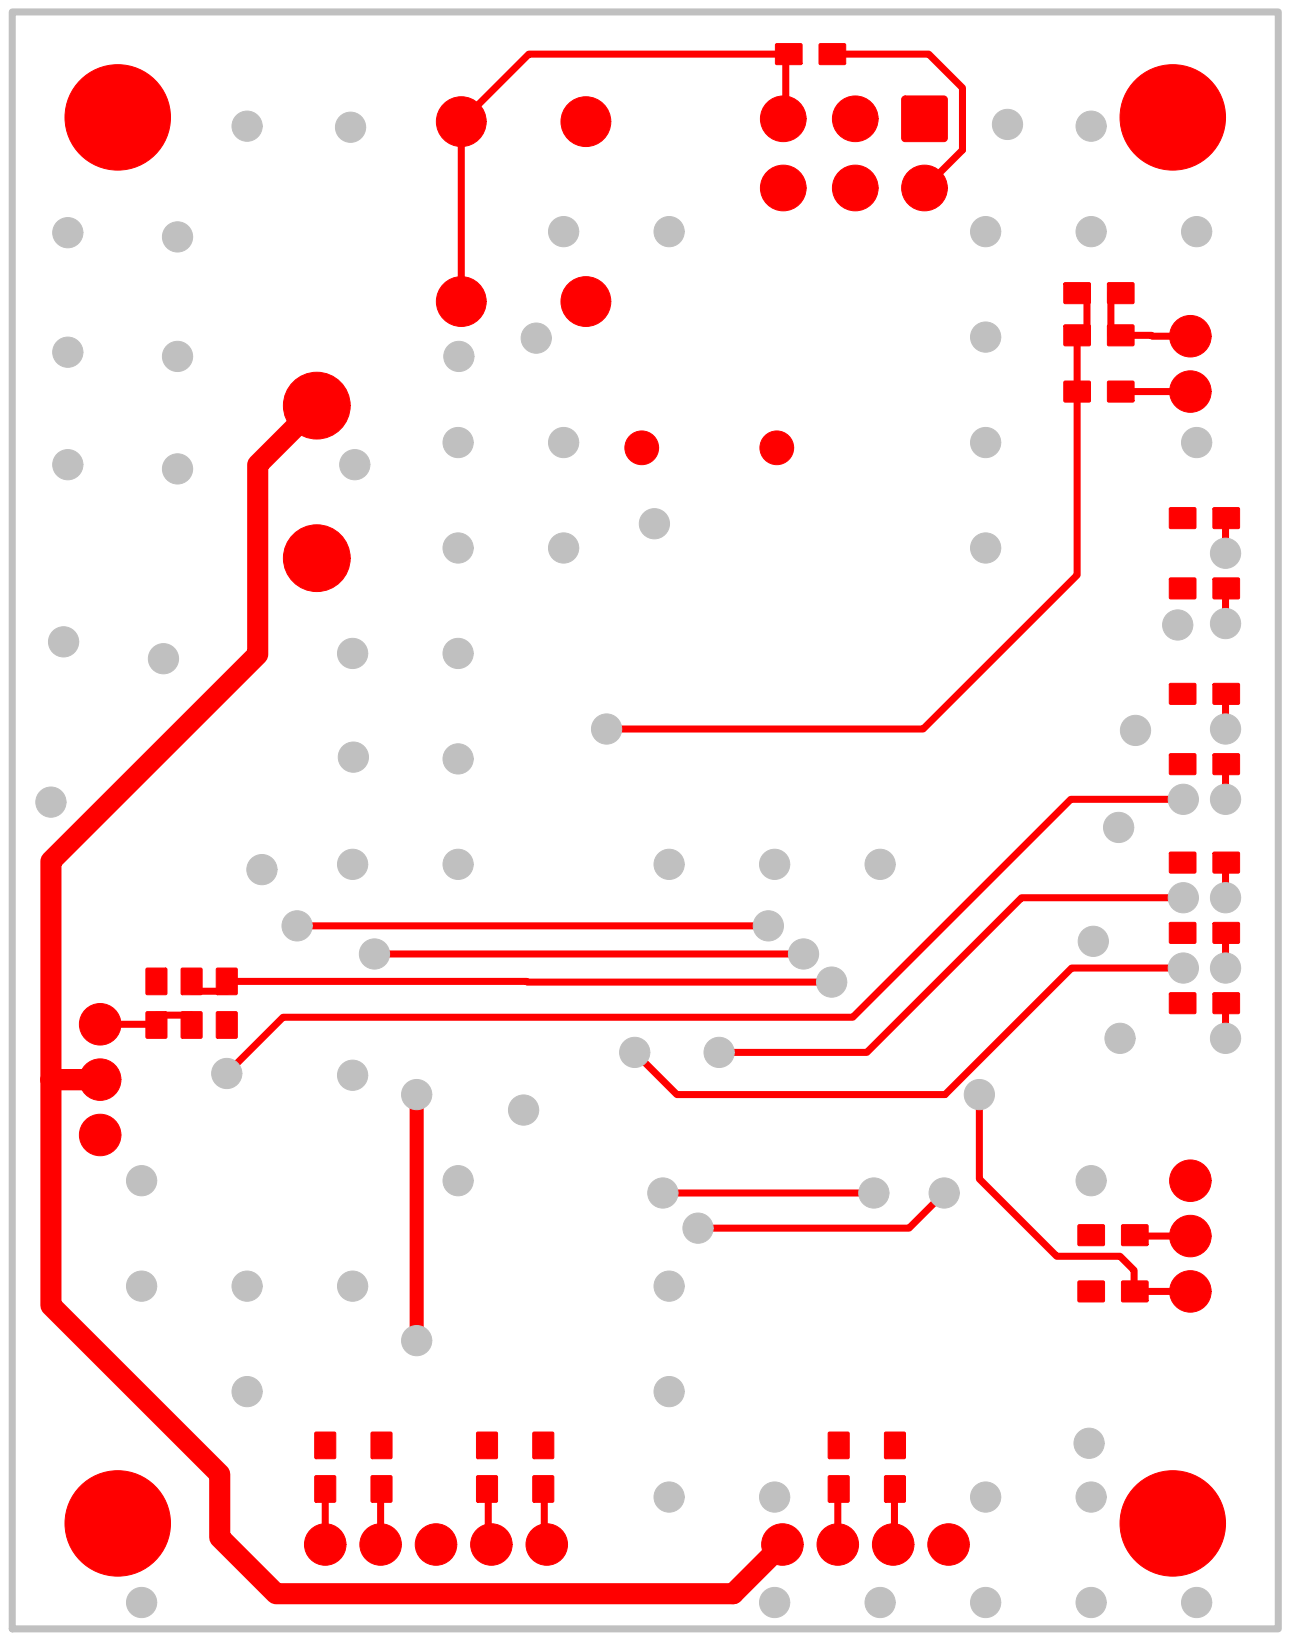
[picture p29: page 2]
R10R¹⁰x1 R¹⁰x2; Y100 Y¹⁰⁰x1; Y¹⁰⁰x2; R15R¹⁵x1 R¹⁵x2; R16R¹⁶x1 R¹⁶x2; R1R¹x1; R¹x2; R2R²x2; R²x1; C3C³x1; C³x2; D1D¹x1 D¹x2; D2D²x1 D²x2; D3D³x1 D³x2; D4D⁴x1 D⁴x2; D5D⁵x1 D⁵x2; D6D⁶x1 D⁶x2; D7D⁷x2; D⁷x1; D8D⁸x2; D⁸x1; X1X¹x1; X3X³x1; X4X⁴x1; R3R³x1; R³x2; R4R⁴x1; R⁴x2; R5R⁵x1; R⁵x2; R6R⁶x1; R⁶x2; R7R⁷x1; R⁷x2; R8R⁸x1; R⁸x2; R9R⁹x1; R⁹x2; SW1SW¹x1 SW¹x2 SW¹x3 SW¹x4 J3J3x1 J3x2

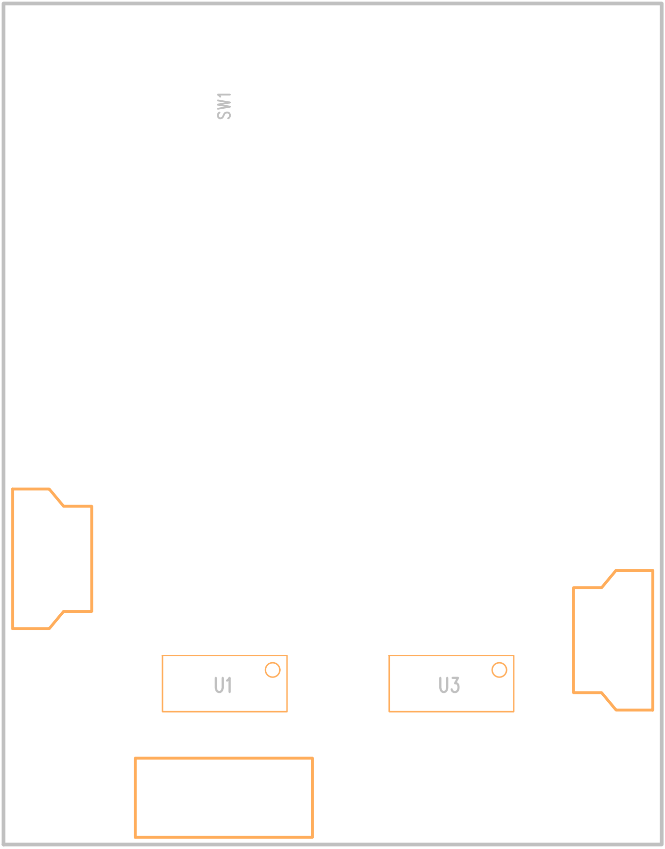
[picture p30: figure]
U3 SW¹; U3 U³x7; U³x6; U³x5; U³x4; U³x3; U³x2; U³x1

R1
C3


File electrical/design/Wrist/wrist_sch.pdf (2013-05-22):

D

6 | 5 | 4 | 3 | 2 | 1


REVISION RECORD

LTR | ECO NO: | APPROVED: | DATE:

CHECKED: <Checked By> | DATED: <Checked Date> | CODE: | SIZE: | DRAWING NO: | REV:

QUALITY CONTROL: <QC By> | DATED: <QC Date>

RELEASED: <Released By> | DATED:

<Scale> SCALE: | 1 2 SHEET: OF

D

6 | 5 | 4 | 3 | 2 | 1


+3.3V | REVISION RECORD

LTR | ECO NO: | APPROVED: | DATE:

DRAWN: <Drawn By> | DATED: <Drawn Date>

CHECKED: <Checked By> | DATED: <Checked Date> | CODE: | SIZE: | DRAWING NO: | REV:

QUALITY CONTROL: <QC By> | DATED: <QC Date>

RELEASED: <Released By> | DATED:

<Scale> SCALE: | 2 2 SHEET: OF

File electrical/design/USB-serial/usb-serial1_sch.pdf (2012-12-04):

# ABD

6


DRAWN: C. Hyman | DATED: 24 Apr 2012

CODE: U | SIZE: B | DRAWING NO: USB-MSER | REV: 1

CHECKED: <Checked By> | DATED: <Checked Date>

RELEASED: <Released By> | DATED:

N/A SCALE: | 1 1 SHEET: OF

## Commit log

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2012-01-08 Added PLL synthesizer design resources. Added SKY65116.pdf UHF PA datasheet. Designed video input LPF.
    [PLL_Loop_Filter_Tool.xls, videoInputLPF.sch]
2012-01-09 Started schematic entry in PADS.
    [MRVTS.sch]
2012-01-09 Began creating library for Rover RF components.
    [MRVTS.sch]
2012-01-09 Added Cody's library and designs
    [armctl_001.sch, bogiectl.sch]
2012-01-14 Added CPC drawings
    [cpc_rev1.sch]
2012-01-15 Added Rev1 CPC final draft
    [cpc_rev1.sch]
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2012-01-16 UHF video transmitter schematic entry. Added SPICE simulation of 4MHz elliptic LPF for video input.
    [MRVTS.sch, videoInputLPF.sch]
2012-01-17 More schematic entry.
    [MRVTS.sch]
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2012-01-23 Added synthesizer loop filter.
    [MRVTS.sch]
2012-01-26 Designed synthesizer loop filter. Schematic entry.
    [MRVTS.sch]
2012-01-26 Beginning to design power supply.
    [MRVTS.sch]
2012-01-27 Designed 3.6V switching regulator. Designed RF PA Bi-Directional coupler detectors.
    [MRVTS.sch]
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2012-01-28 Power supply design.
    [MRVTS.sch]
2012-02-01 Designing the digital bits. No pun intended.
    [MRVTS.sch]
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2012-02-04 Uploaded some schematics and layouts and libraries and such for safekeeping
    [bogiectl2.sch, cpc_rev1.sch, cpc_rev2.sch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]
2012-02-04 Designing 900MHz RF front end.
    [900MHzRFE.sch]
2012-02-05 Uploaded motor driver/solenoid designs/datasheets
    [solenoid_driver_rev1.sch, xbee_cam_interface_rev1.sch]
2012-02-05 Designing video MUX.
    [videoMux.sch]
2012-02-06 Wrote some AX-12 programming firmware to be used with AX-12s that are operating at 1Mbaud.
    [900MHzRFE.sch]
2012-02-06 Working on the video MUX.
    [videoMux.sch]
2012-02-07 designing video MUX and 900MHz front end.
    [4MHz5OLPF.sch, 900MHzRFE.sch, MRVTS.sch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]
2012-02-08 Added electrical box layout
    [bogiectl2.sch, cpc_rev2.sch, solenoid_driver_rev1.sch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]
2012-02-09 75% done with video MUC PCB layout. Designed 4MHz 5th order elliptic LPF for 75 ohm system.
    [4MHz5OLPF.sch, videoMux.sch]
2012-02-10 Video MUX layout.
    [videoMux.sch]
2012-02-11 Testing RS-485 termination methods.
    [test1a.CSV, test1b.CSV, test2a.CSV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]
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2012-02-21 Finished routing video MUX PCB REV0.
    [900MHzRFE.sch, videoMux.sch]
2012-02-25 Putting final touches on video MUX PCB.
    [videoMux.sch]
2012-03-07 Designing balanced audio receiver for video MUX.
    [videoMux.sch]
2012-03-08 Added balanced audio receiver to video MUX. Finished checking DFM issues.
    [videoMux.sch]
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2012-03-09 Making changes to video MUX per my own design review. Updated arm electronics block diagram (not entirely up to date yet).
    [videoMux.sch]
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2012-03-09 Setting up CAM for video MUX.
    [videoMux.sch]
2012-03-09 more CAM.
    [DRL.drl]
2012-03-11 Finished generating CAM files. Ordered PCB from this revision.
    [videoMux.sch]
2012-03-20 Solenoid driver
    [solenoid_driver_rev2.sch]
2012-03-20 CPC updates
    [cpc_rev2.sch]
2012-03-20 Bogie controller updates
    [bogiectl2.sch]
2012-03-23 Updated multiple boards
    [bogiectl2.sch, solenoid_driver_rev2.sch, xbee_cam_interface_rev2.sch]
2012-03-24 Started schematic entry for the tripod interface.
    [tripod.sch]
2012-03-26 Updated CPC
    [cpc_rev2.sch, xbee_cam_interface_rev2.sch]
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2012-03-28 Added bogie controller PCB updates
    [bogiectl2.sch, cpc_rev2.sch]
2012-03-29 Made a panel!
    [bogiectl2.sch, cpc_rev2.sch, xbee_cam_interface_rev2.sch]
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2012-04-02 Schematic entry for the tripod interface.
    [tripod.sch]
2012-04-02 Schematic entry for tripod interface.
    [tripod.sch]
2012-04-03 More tripod schematic entry. Added microphone pre amplifier simulation.
    [tripod.sch]
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2012-04-14 Updated tripod.
    [tripod.sch]
2012-04-14 Tripod PCB layout.
    [tripod.sch]
2012-04-16 Finished layout and routing for tripod interface.
    [tripod.sch]
2012-04-18 Managing ground planes.
    [tripod.sch]
2012-04-18 Working on tripod. Done with plane management, passed DRC, reviewing design.
    [tripod.sch]
2012-04-19 Finished tripod "self" design review. Generated CAM files.
    [tripod.sch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]
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2012-04-27 Wrist design entry.
    [wrist.sch]
2012-04-28 More wrist design entry.
    [wrist.sch]
2012-05-16 Added bogie ctl rev 3
    [bogiectl2.sch, bogiectl3.sch]
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2012-10-20 Started new packet router. Layout not finished. Added 46-pin header to rover library.
    [cpc_rev3.sch]
2012-10-24 Packet Router layout is good, but nets need to be routed.
    [cpc_rev3.sch]
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2012-10-27 Packet Router: Ready for review
    [cpc_rev3.sch]
2012-12-04 Added schematics and BOMs for most electrical boards
    [bogiectl3.sch]
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2013-04-07 Added Rev4 of central packet router board.
    [cpc_rev4.sch]
2013-04-07 Added CAM files for packet router, modified silkscreen on pcb file a little.
    [NCDrill.drl]
2013-04-12 Final revisions to central packet router rev4.
    [NCDrill.drl]
2013-04-24 Finished inital routing and DRC checks of wrist board. Still need to lay out silk screen.
    [wrist.sch]
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2013-04-26 Final revisions to wrist board.
    [wrist.sch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]
2013-04-30 Final changes to wrist board, changed vin connector to right angle connector.
    [wrist.sch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]
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
